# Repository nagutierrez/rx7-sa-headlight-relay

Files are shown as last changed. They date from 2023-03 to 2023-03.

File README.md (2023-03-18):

# RX-7 SA Headlight Relay Board

A replacement headlight assembly relay board for the 1979-1980 Mazda RX-7.

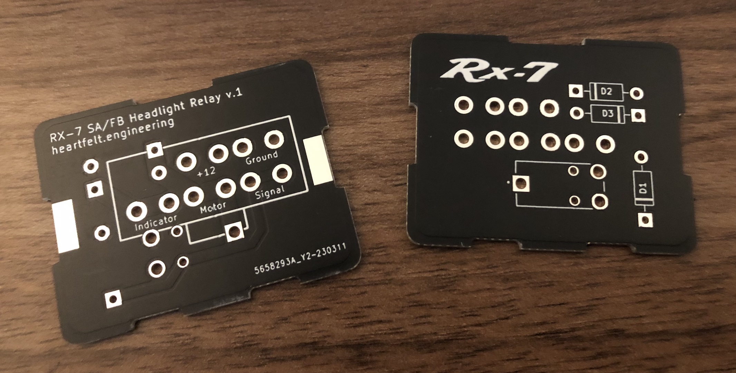
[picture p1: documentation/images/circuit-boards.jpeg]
circuit boards

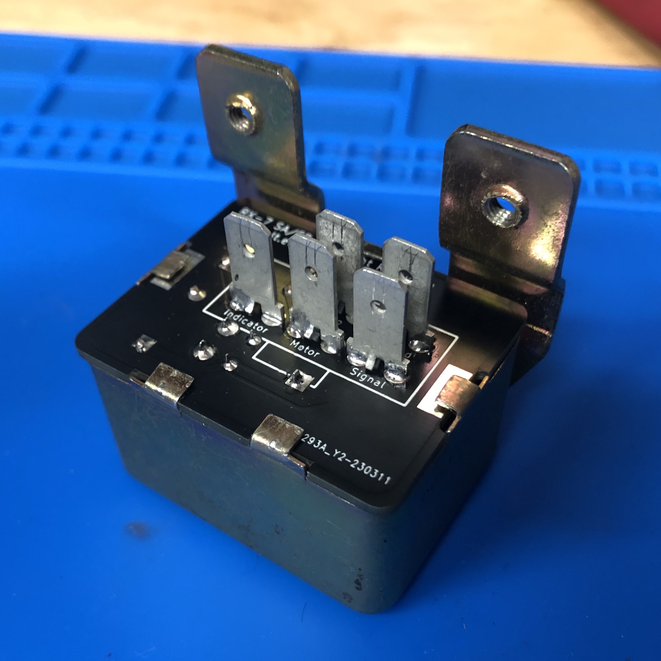
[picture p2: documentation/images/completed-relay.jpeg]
completed relay

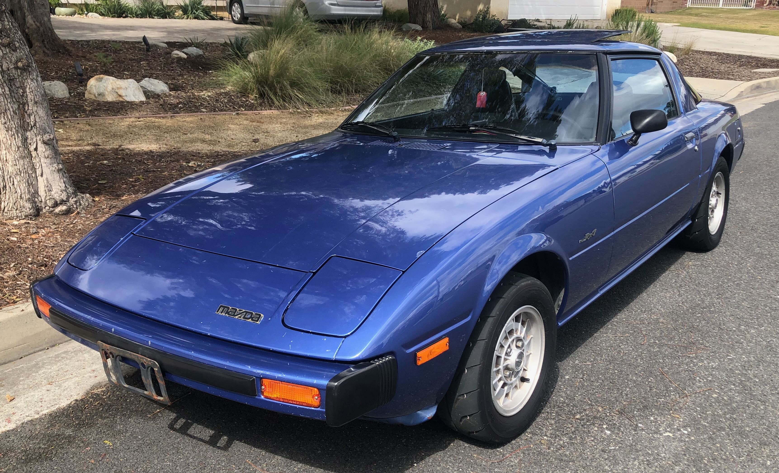
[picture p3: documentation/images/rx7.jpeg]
rx7


## Context

The first generation Mazda RX-7 SA (79-80) features a self-contained pop-up headlight assembly. This assembly contains the sensor and relay necessary to correctly position itself in the up or down position dependent on signal.

After decades of operation the relay in this assembly may fail, causing the headlight to no longer go up and down, or do so intermittently. While this relay could be replaced with a generic automotive relay, some functionality could be lost as it includes an additional diode protected output for the dashboard headlight indicator.

This project defines a replacement board with modern easily sourcable parts that maintains original functionality with no modifications necessary to wiring and no visible changes.

## Prerequisit Reading

Please understand the RX-7 wiring diagram before attempting any electrical work!

Original Source: http://www.wright-here.net/files/manuals/1979RX7WiringDiagram.pdf

Archive for posterity: https://archive.org/details/1979-rx-7-wiring-diagram

## Sections

- [Teardown](./documentation/00-teardown.md)
- [Design](./documentation/01-design.md)
- [Parts](./documentation/02-parts.md)
- [Construction](./documentation/03-construction.md)

## Directory Structure

- `documentation` - documentation for the project
- `hardware` - KiCad hardware design files
- `production` - production files for the PCB (zip this up and send it to your favorite PCB manufacturer)

## Caveats

- I suspect this will work with the FB RX-7 but cannot verify since the headlight assembly appears to be slightly different
- This was my first PCB project
- Please understand what you are doing; I bear no responsibility for any damage you may cause to yourself or your vehicle
- Manufacturing of the board is not included in the scope of this project; there are plenty of low cost pcb manufacturers that can guide you through the process

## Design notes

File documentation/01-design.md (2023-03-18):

# Design

The circuit board was designed to fit into the housing of the original relay and provide the same connections.

## Connections

The first order of business was to trace the wiring of the connector. Because it is part of the headlight assembly, it was not detailed in the RX-7 wiring diagram.

Using the color codes indicated defined in the wiring diagram, the connections were traced as follows:

```
Pin numbers when looking at the connector from the side of the wires
__|-|__
|1 2 3|
|4 5 6|
-------
```

| Pin | Color | Function  | Description |
| --- | --- | --- | --- |
| 1 | G (Green) | Signal | The signal from the sensor; High = motor on, Low = motor off |
| 2 | W (White) | Motor | The output to provide 12 volts to the motor |
| 3 | YG (Yellow, green stripe) | Indicator | The diode protected output to the dashboard indicator |
| 4 | B (Black) | Ground | The ground connection for the motor |
| 5 | WR (White, red stripe) | 12V | The constant 12 volt power connection |
| 6 | | | No connection |

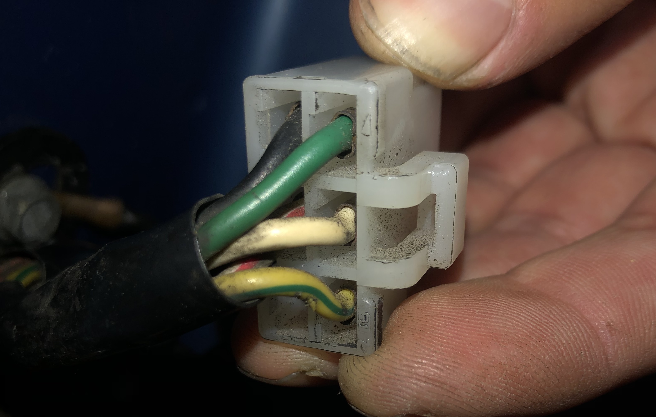
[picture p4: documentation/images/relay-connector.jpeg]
connector


## Schematic

With the connection traced, the schematic was designed.

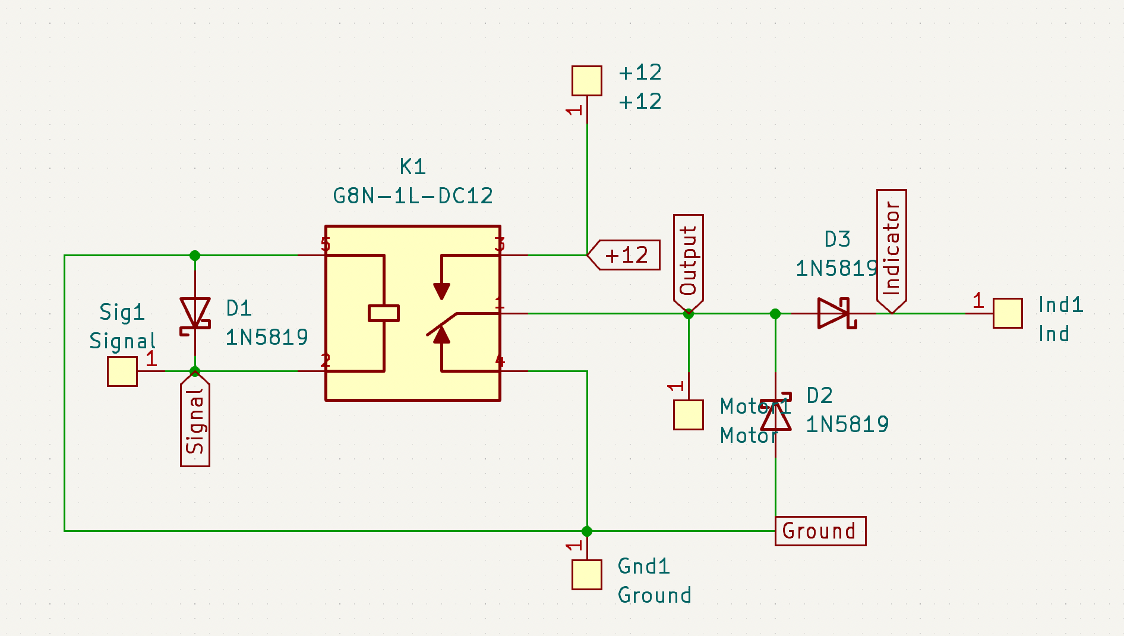
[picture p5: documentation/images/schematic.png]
schematic


The configuration of the schematic matches that of the original; the relay `K1` switches the motor between ground and 12 volts. The output of the relay, pin 1, feeds the motor directly. The dashboard indicator light is fed through diode `D3` in order to prevent current from flowing back through the motor from the other headlight.

Diodes `D1` and `D2` are flyback diodes to prevent voltage spikes from the inductive loads of the relay and motor coil; though not included in the original design and technically optional, these will help extend the lives of both the driver's light switch and relay contacts and add minimal cost.

## Layout

The physical layout of the PCB and components was primarily dictated by the dimensions of the original relay enclosure, connector, and desire to keep high current traces short and fat. A two layer circuit board was used for ease of routing.

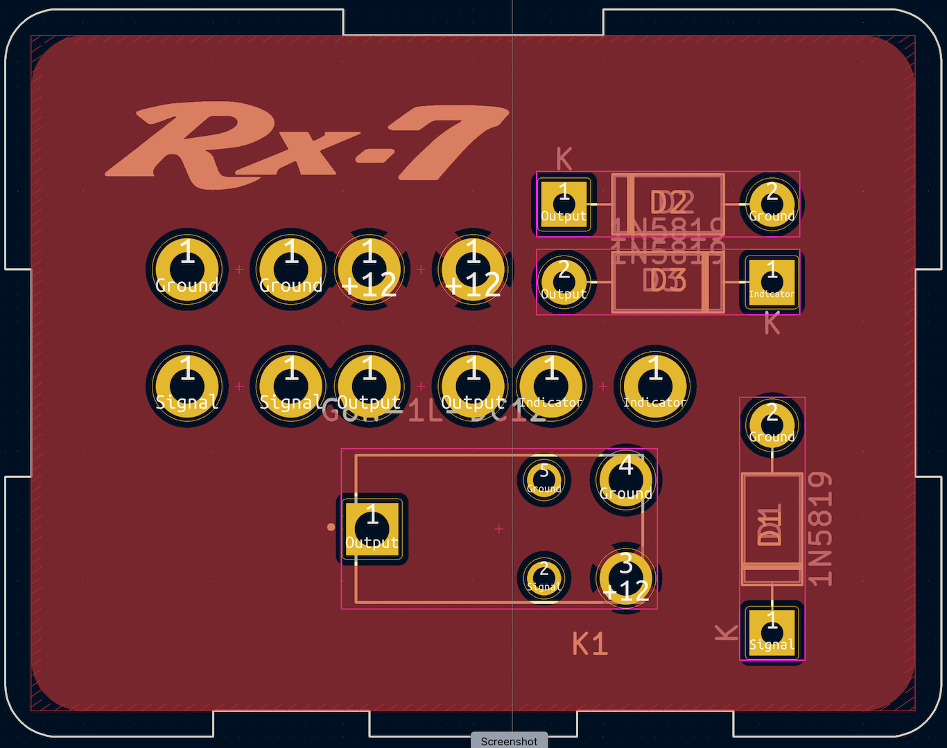
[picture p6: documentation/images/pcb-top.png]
pcb top


The top layer of the PCB, which is intended to be protected inside the original relay's metal housing, contains the components and a power plane. The power plane ensures the least resistance for the high current connections between 12V and the motor output.

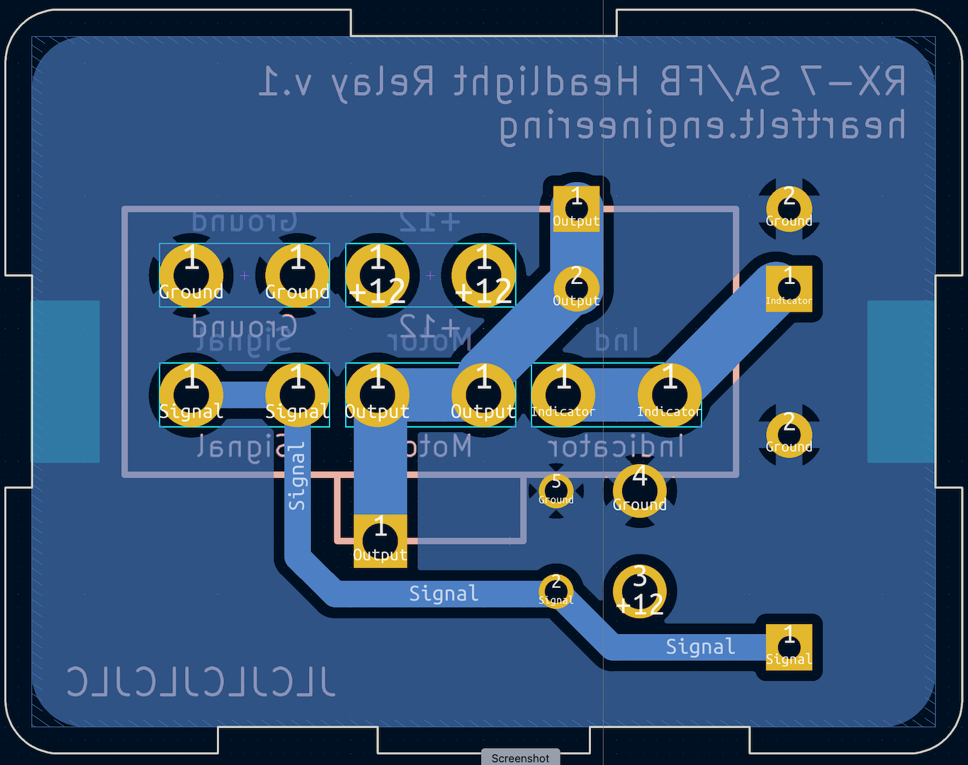
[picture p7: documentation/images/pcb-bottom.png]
pcb bottom


The bottom layer includes the connector and associated routing, all surrounded by a ground plane. Once again a ground plane was used to provide as low resistance as possible. Traces were also made as wide as possible given the space constraints caused by the connector. The silkscreen of the connector with the locking tab was included to indicate proper orientation of the 6 pin connector.

Continue to [parts](./02-parts.md).

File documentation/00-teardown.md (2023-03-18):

# Teardown

## Headlight Assembly

The headlight assembly in the early RX-7 consists of a geared DC motor with integrated sensor and attached relay. When replacing the relay, one does not need to remove the assembly entirely (unless you want to clean it and relubricate it, which isn't a bad idea after 40 years).

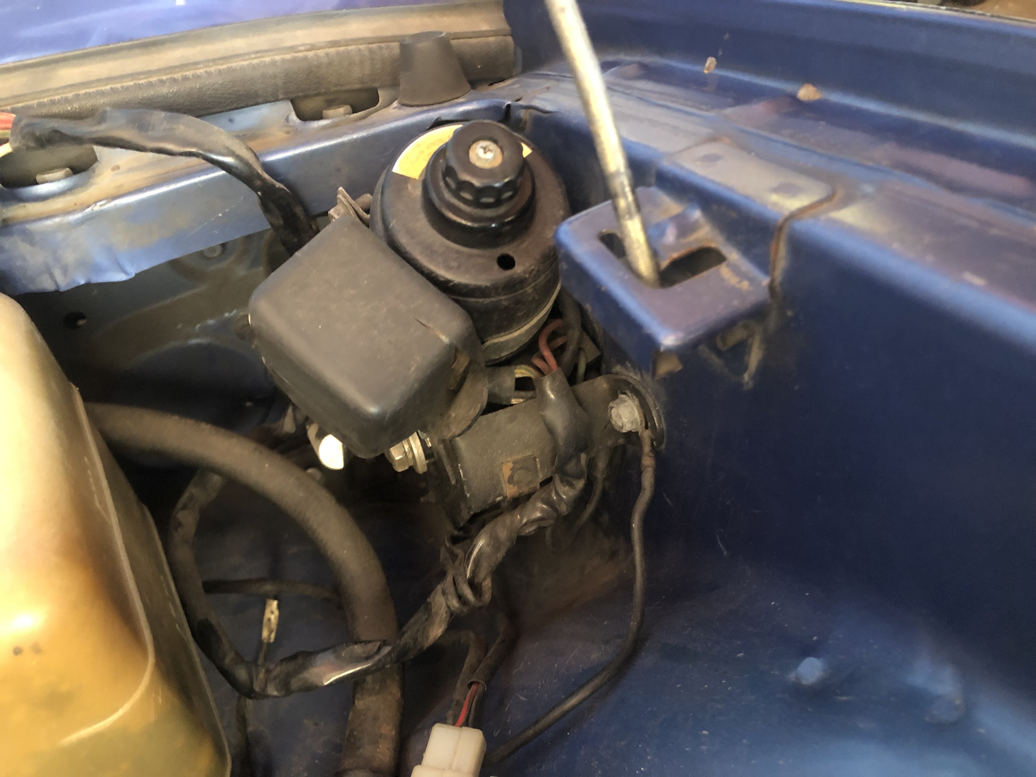
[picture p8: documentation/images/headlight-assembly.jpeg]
headlight assembly


The relay, which is enclosed in the black rubber sleeve, is attached to the motor assembly via a circular metal bracket and a 6 pin connector. Gently push back the sleeve to reveal the connector (note the sleeve will likely rip if it hasn't already).

connector

Once unplugged and the bracket loosened, it may be removed from the assembly, two philips screws can be removed to separate the bracket from the relay and sleeve. The sleeve may then be removed and you will be left with the original relay.

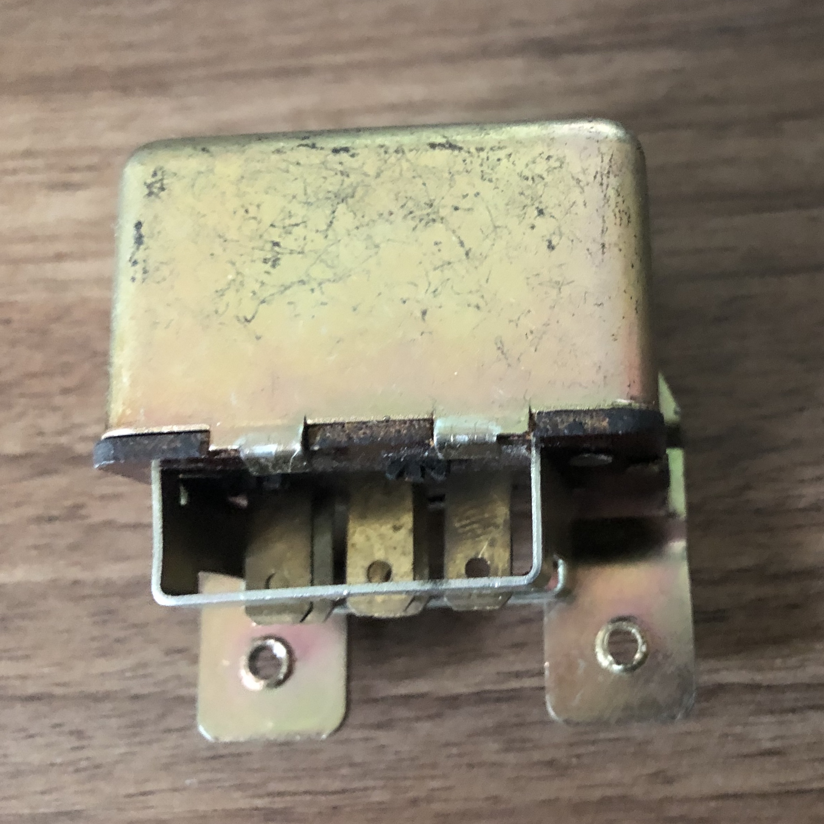
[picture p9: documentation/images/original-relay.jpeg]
headlight relay


After bending the enclosure tabs, one can remove the board with the terminals and relay. With the metal enclosure removed, one can see the relay contacts. An attempted cleaning using emery paper resulted in slightly better performance, but did not make the headlight reliable.

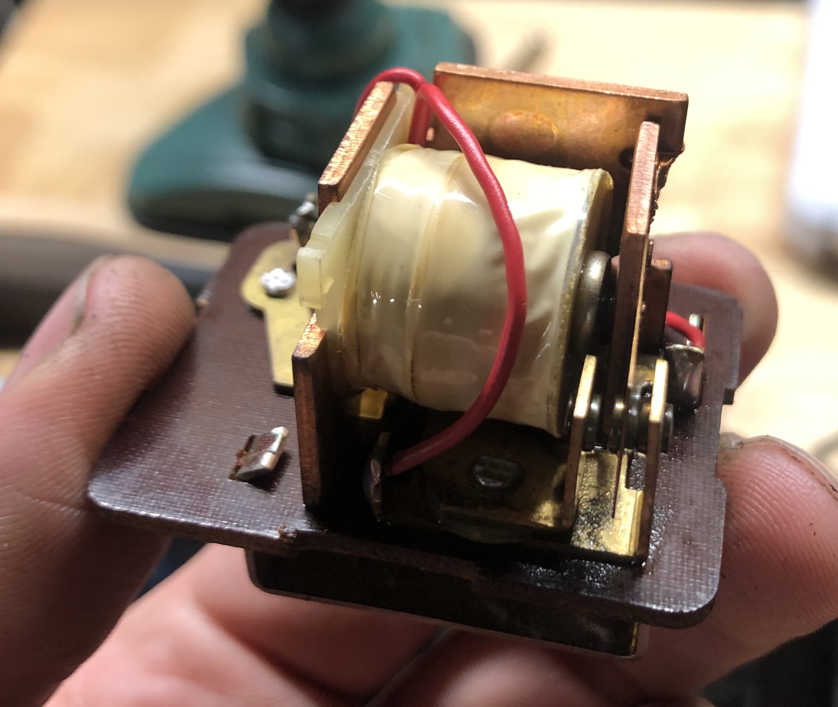
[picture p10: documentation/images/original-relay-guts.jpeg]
headlight relay internals


This circuit board was used as the basis for the design of the replacement board detailed in [the next section](./01-design.md).

## Errata

The sensor portion of the motor is located under the circular rubber cab with three wires going in. In the schematic, this is represented as the switch within a circle with the two diodes leading into it. In hardware, this consists of three circular tracks and the switch contacts which rotate with the motor output shaft. Depending on the position of the shaft, the contacts will be made or broken, providing or removing power from the motor respectively.

Continue to [design](./01-design.md)

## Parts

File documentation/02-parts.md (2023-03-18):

# Parts

The following parts were chosen for this project

| Part # | Qty | Description | Manufacturer |
| --- | --- | --- | --- |
| 19705-4001 | 5 | Male Tab Terminal | Molex |
| G8N-1L-AS DC12 | 1 | Relay | Omron |
| 1N5819 | 3 | Schottky Diodes | STMicroelectronics |

## Tab Terminals

These terminals were the right dimensions to work with the original connector and could be mounted directly onto the PCB.

## Relay

The omron relay was chosen for its compact size, high current capacity, and availability. It was designed specifically for use with DC motors in automotive applications.
https://omronfs.omron.com/en_US/ecb/products/pdf/en-g8n.pdf

## Diodes

The 1N5819 Schottky diodes were chosen for their low forward voltage drop and high current capacity. Their quick response time make them a good choice for flyback diodes, while their current capacity is will ensure that they are not ruined by the current draw of the indication light.

Continue to [construction](./03-construction.md)

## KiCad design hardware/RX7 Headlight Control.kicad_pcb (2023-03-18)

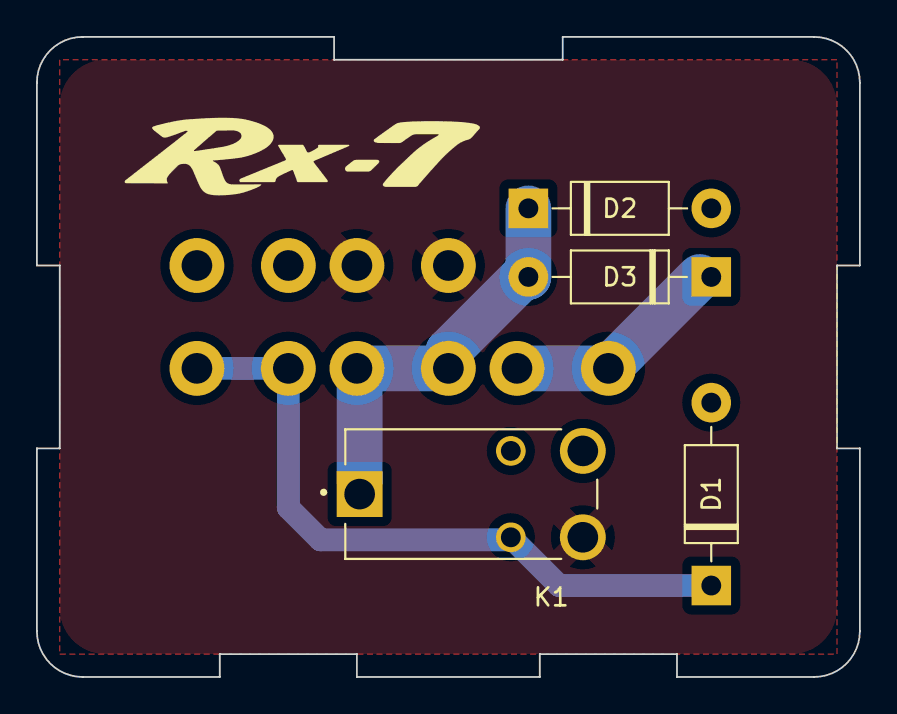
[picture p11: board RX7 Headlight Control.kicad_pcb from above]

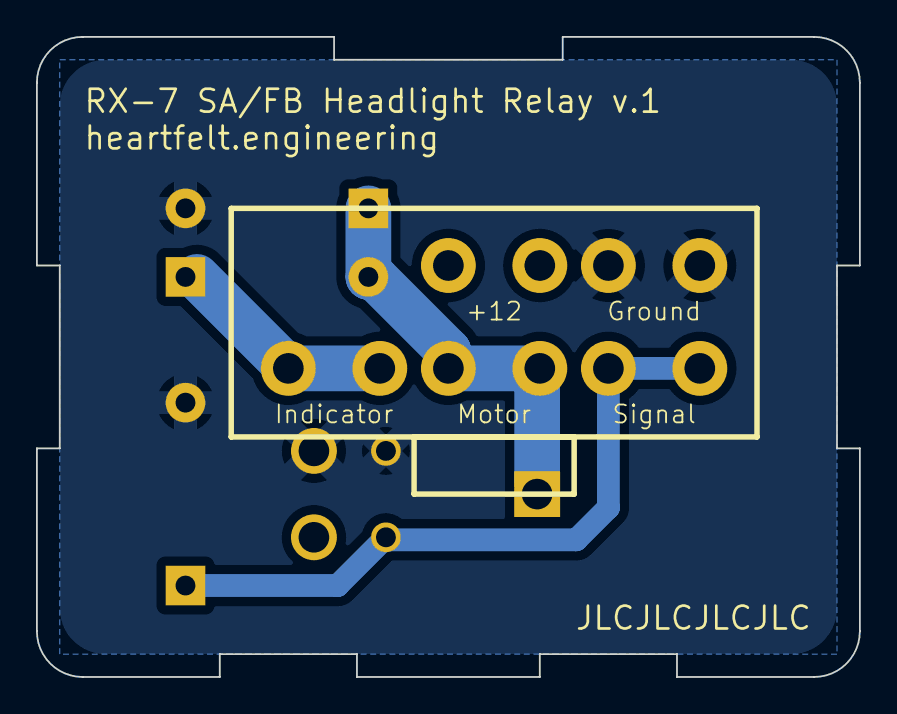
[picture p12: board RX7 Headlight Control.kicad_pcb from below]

Board: 2 copper layers, 45.7 x 35.6 mm, 9 parts (5 on the bottom side), 5 nets.

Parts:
+12: +12; Molex_197054001
D1, D2, D3: 1N5819; D_DO-41_SOD81_P10.16mm_Horizontal
Ground: Ground; Molex_197054001
Indicator: Ind; Molex_197054001
K1: G8N-1L-DC12; RELAY_G8N-1L-DC12
Motor: Motor; Molex_197054001
Signal: Signal; Molex_197054001

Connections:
+12: +12.1, K1.3
Ground: D1.2 (A), D2.2 (A), Ground.1, K1.4, K1.5
Indicator: D3.1 (K), Indicator.1
Output: D2.1 (K), D3.2 (A), K1.1, Motor.1
Signal: D1.1 (K), K1.2, Signal.1

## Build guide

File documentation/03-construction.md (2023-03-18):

# Construction

With PCB and parts in hand, we can now begin populating the board.

## Bottom Layer

### Terminal Connections

I suggest first soldering the terminal tab connections, as these require a good amount of heat.

With the board mounted in a vice bottom side up, I tacked each terminal in place with a small amount of solder to one of the two pins. Once they were all tacked in place, I flipped the board over so that the top component side faced upward and soldered them fully. Remember to solder the unsoldered terminal first or the terminal may fall out of the board.

This was tedious; a future improvement would be to 3d print a fixture to hold all 5 terminal tabs in alignment so they can be soldered in one go.

## Top Layer

### Diodes

Next on the top layer of the board, the diodes were then soldered in place, and their leads cut flush. Make sure to match the polarity of the diodes to that printed on the PCB silkscreen.

### Relay

Finally the relay should be soldered in place; be sure all 5 connections are made.

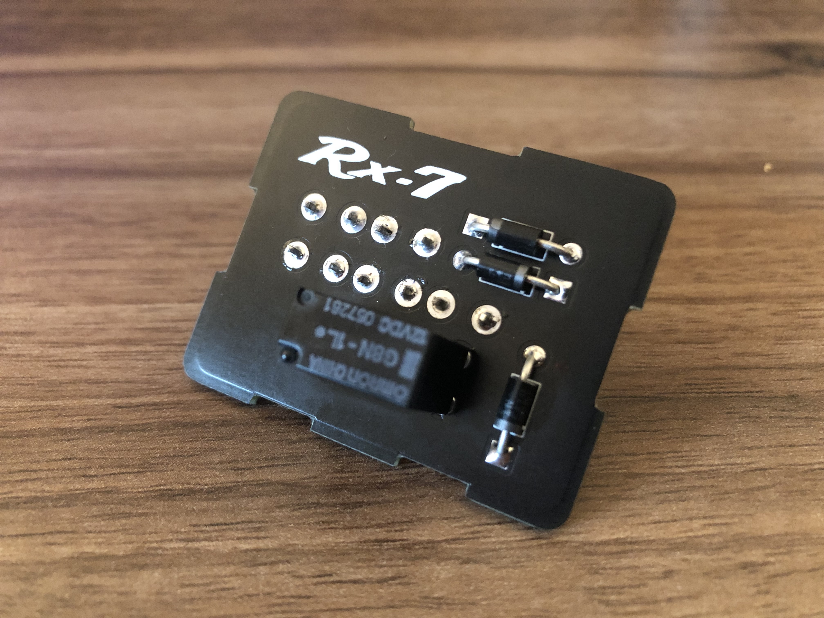
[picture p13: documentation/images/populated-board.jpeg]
top layer of populated board


## Testing

Before inserting the board into the relay housing, it is a good idea to test the board to make sure it works. Connect it to the original headlight wiring harness and switch on the headlights; The headlights should rise and lower as expected.

## Housing

Now the completed board may be inserted into the original relay housing. Fold the tabs back over to retain the board in place, and the rest of reassembly is the reverse of tear down.

board in housing
